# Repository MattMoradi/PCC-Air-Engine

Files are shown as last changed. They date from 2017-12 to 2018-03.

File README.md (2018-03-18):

# PCC-Air-Engine

Tired of those darn old hand drawn designs for the PCC Air Engine project? Think you deserve better? Well here you are.

This repository contains all of the necessary files for the PCC Air Engine project from designs to gcode. All CAD modeling and CAM toolpathing was done using Autodesk Inventor HSM. Special thanks to Autodesk for providing this software free to students. All NC code has been optimized to run on the HAAS Mini-Mill 2005. This also contains the new standardized digital drawing file format and has replaced the previous hand drawn ones at Glencoe.

### Included Parts & Formats: ###

* Standard: CAD + CAM + DWG + PDF + CNC
* Standard_Bushing: CAD
* Piston_Bushing: CAD
* Piston: CAD + DWG + PDF
* Piston_Block (Cylinder): CAD + CAM + DWG + PDF + CNC
* Flywheel: CAD + DWG + PDF
* Crankshaft: CAD + DWG + PDF
* Air_Engine_Full: CAD + ASM

### PCC Credits Covered ###
* CRN: 11691 - MCH100-0
* CRN: 11691 - MCH135-0
* CRN: 11692 - MCH145-0
* CRN: 11964 - MCH150-0
* CRN: 11693 - MCH160-0
* CRN: 11694 - MCH180-0
* CRN: 11965 - MCH205-0

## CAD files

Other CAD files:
DWG Drawings/Flywheel_Draw.dwg
DWG Drawings/CrankShaft_Draw.dwg
DWG Drawings/Piston_Block_Draw.dwg
DWG Drawings/Piston_Draw.dwg
DWG Drawings/Standard_Draw.dwg
OldVersions/Piston_Draw.0006.dwg
OldVersions/Flywheel_Draw.0004.dwg
OldVersions/Standard_Draw.0020.dwg
OldVersions/CrankShaft_Draw.0005.dwg
OldVersions/Piston Block_Draw.0007.dwg
Air_Engine_ASM.iam
CrankShaft.ipt
CrankShaft_Mill.ipt
Flywheel.ipt
OldVersions/Air_Engine_ASM.0010.iam
OldVersions/CrankShaft Mill.0001.ipt
OldVersions/CrankShaft.0006.ipt
OldVersions/CrankShaft_Mill.0002.ipt
OldVersions/Flywheel.0003.ipt
OldVersions/Main Block.0001.ipt
OldVersions/Piston Block.0011.ipt
OldVersions/Piston.0002.ipt
OldVersions/Standard.0026.ipt
Piston.ipt
Piston_Block.ipt
Piston_Bushing.ipt
Standard.ipt
Standard_Bushing.ipt

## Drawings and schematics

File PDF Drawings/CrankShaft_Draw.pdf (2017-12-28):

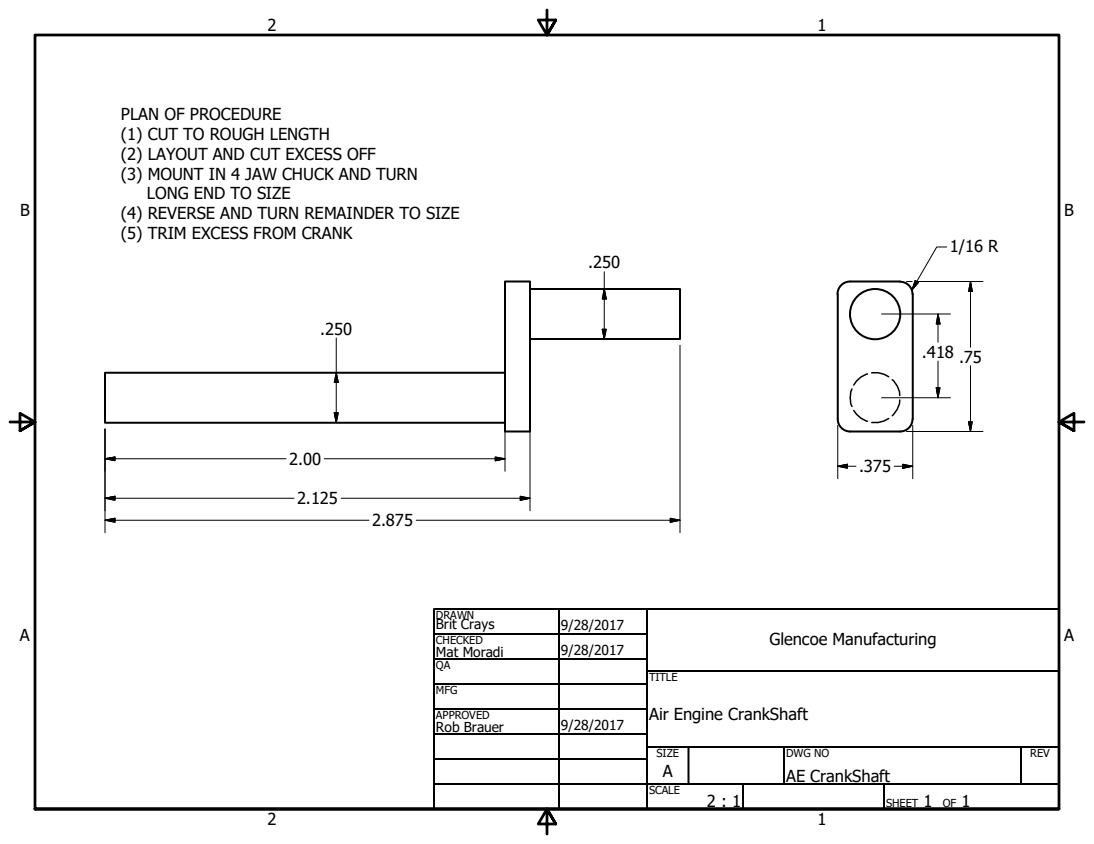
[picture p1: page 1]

PLAN OF PROCEDURE
(1) CUT TO ROUGH LENGTH
(2) LAYOUT AND CUT EXCESS OFF
(3) MOUNT IN 4 JAW CHUCK AND TURN
LONG END TO SIZE
(4) REVERSE AND TURN REMAINDER TO SIZE
(5) TRIM EXCESS FROM CRANK

DRAWN Brit Crays | 9/28/2017 | Glencoe Manufacturing

CHECKED Mat Moradi | 9/28/2017

MFG

APPROVED Rob Brauer | 9/28/2017

Air Engine CrankShaft

SIZE A | DWG NO AE CrankShaft | REV

SCALE 2 : 1 | | SHEET 1 OF 1

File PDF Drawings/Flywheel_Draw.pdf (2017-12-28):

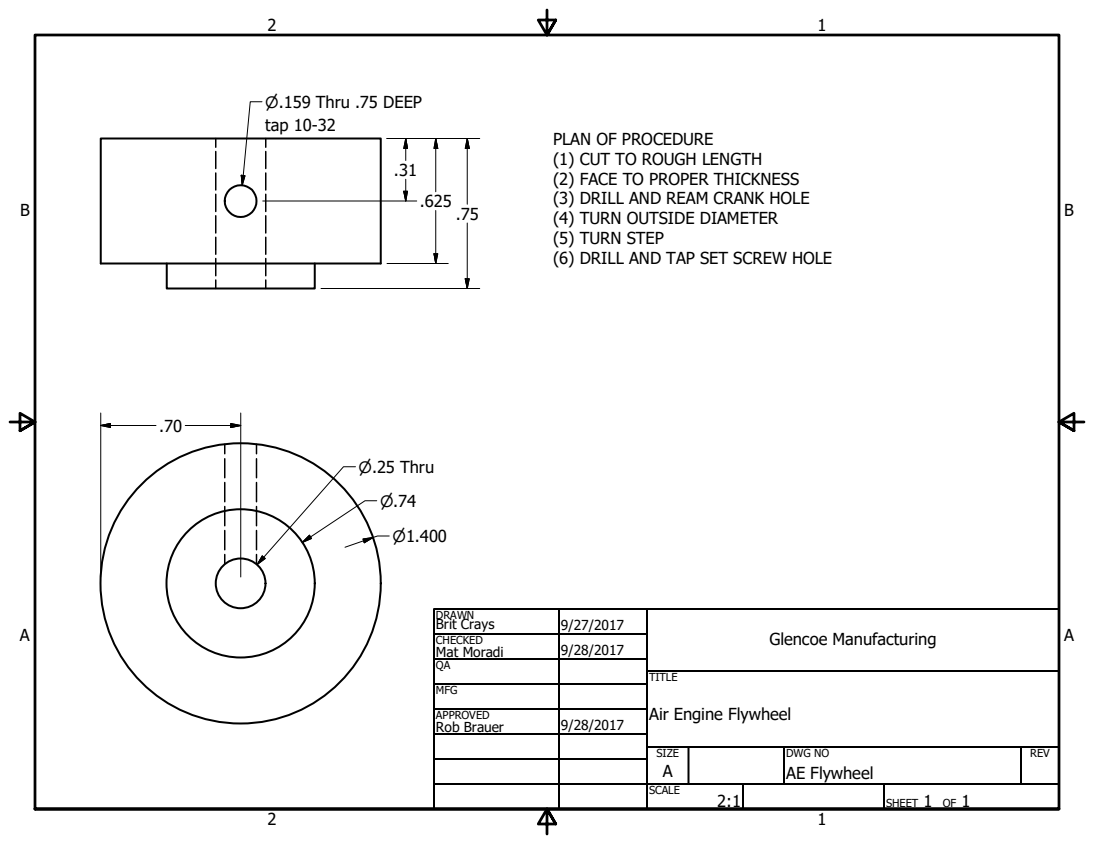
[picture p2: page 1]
tap 10-32

PLAN OF PROCEDURE
(1) CUT TO ROUGH LENGTH
(2) FACE TO PROPER THICKNESS
(3) DRILL AND REAM CRANK HOLE
(4) TURN OUTSIDE DIAMETER
(5) TURN STEP
(6) DRILL AND TAP SET SCREW HOLE

DRAWN Brit Crays | 9/27/2017 | Glencoe Manufacturing

CHECKED Mat Moradi | 9/28/2017

MFG

APPROVED Rob Brauer | 9/28/2017

Air Engine Flywheel

SIZE A | DWG NO AE Flywheel | REV

SCALE 2:1 | | SHEET 1 OF 1

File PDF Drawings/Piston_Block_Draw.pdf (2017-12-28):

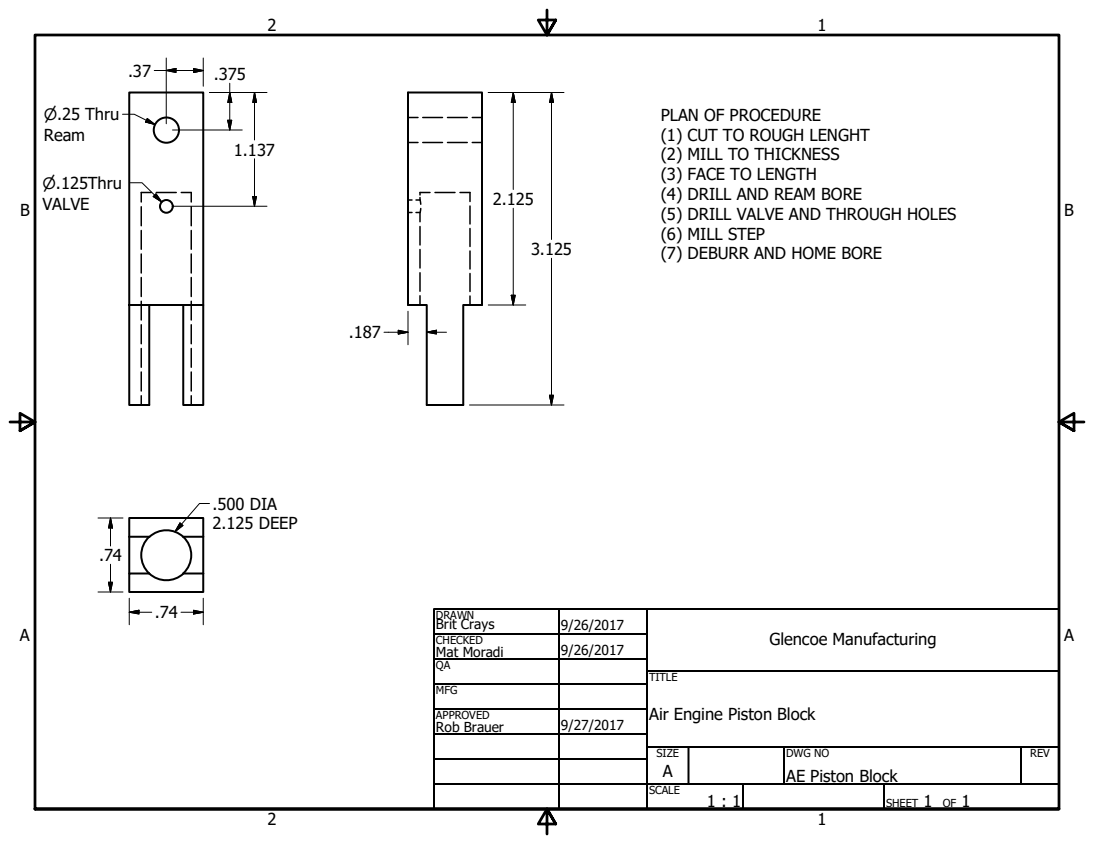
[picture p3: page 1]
.500 DIA 2.125 DEEP

PLAN OF PROCEDURE
(1) CUT TO ROUGH LENGHT
(2) MILL TO THICKNESS
(3) FACE TO LENGTH
(4) DRILL AND REAM BORE
(5) DRILL VALVE AND THROUGH HOLES
(6) MILL STEP
(7) DEBURR AND HOME BORE

DRAWN Brit Crays | 9/26/2017 | Glencoe Manufacturing

CHECKED Mat Moradi | 9/26/2017

MFG

APPROVED Rob Brauer | 9/27/2017

Air Engine Piston Block

SIZE A | DWG NO AE Piston Block | REV

SCALE 1 : 1 | | SHEET 1 OF 1

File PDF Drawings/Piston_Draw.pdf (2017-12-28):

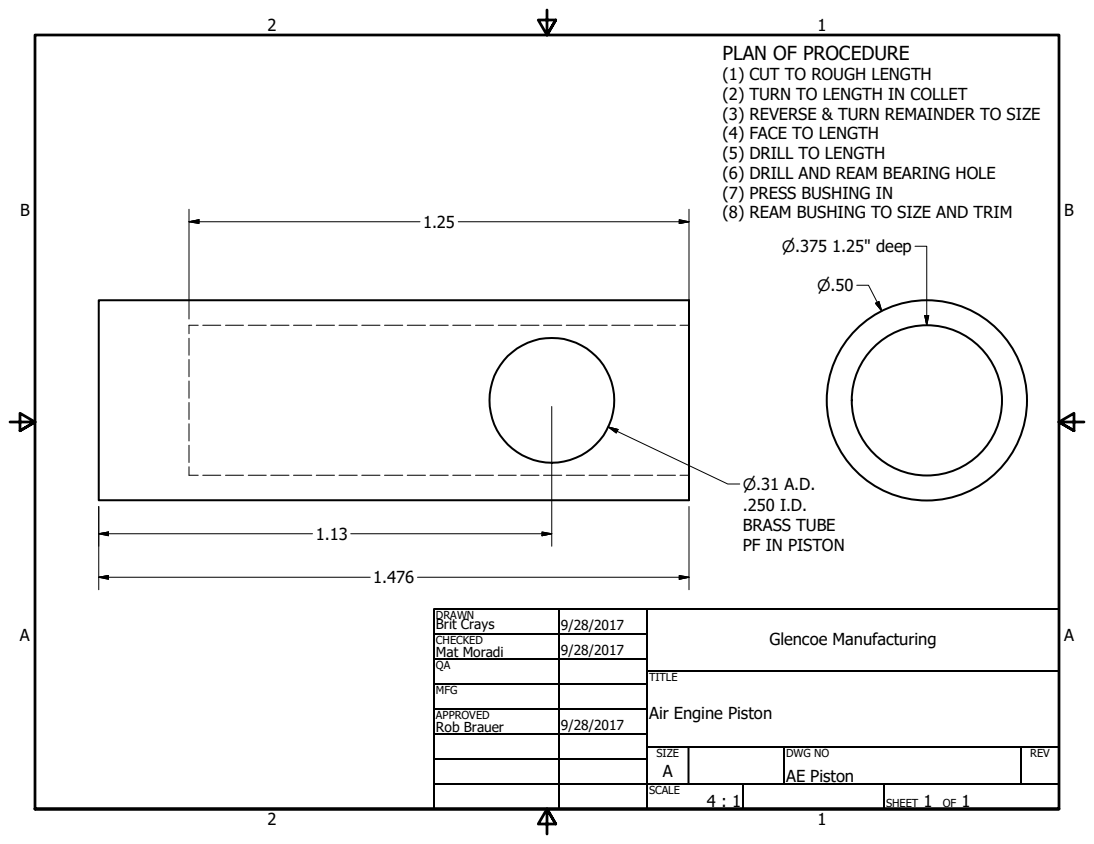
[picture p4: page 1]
.250 I.D. BRASS TUBE PF IN PISTON

PLAN OF PROCEDURE
(1) CUT TO ROUGH LENGTH
(2) TURN TO LENGTH IN COLLET
(3) REVERSE & TURN REMAINDER TO SIZE
(4) FACE TO LENGTH
(5) DRILL TO LENGTH
(6) DRILL AND REAM BEARING HOLE
(7) PRESS BUSHING IN
(8) REAM BUSHING TO SIZE AND TRIM

DRAWN Brit Crays | 9/28/2017 | Glencoe Manufacturing

CHECKED Mat Moradi | 9/28/2017

MFG

APPROVED Rob Brauer | 9/28/2017

Air Engine Piston

SIZE A | DWG NO AE Piston | REV

SCALE 4 : 1 | | SHEET 1 OF 1

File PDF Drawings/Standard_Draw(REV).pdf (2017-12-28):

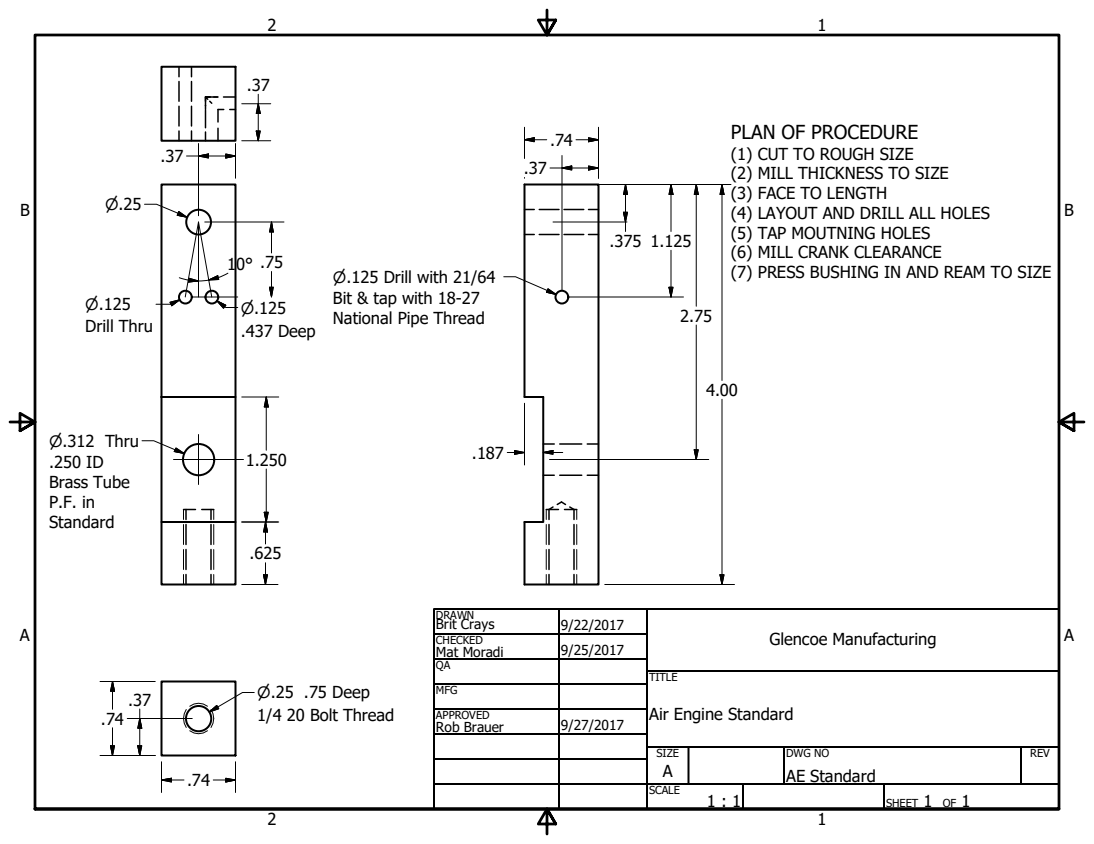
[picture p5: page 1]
1/4 20 Bolt Thread; Drill Thru; .437 Deep; .250 ID Brass Tube P.F. in

PLAN OF PROCEDURE
(1) CUT TO ROUGH SIZE
(2) MILL THICKNESS TO SIZE
(3) FACE TO LENGTH
(4) LAYOUT AND DRILL ALL HOLES
(5) TAP MOUTNING HOLES
(6) MILL CRANK CLEARANCE
(7) PRESS BUSHING IN AND REAM TO SIZE

.125 Drill with 21/64
Bit & tap with 18-27
National Pipe Thread

DRAWN Brit Crays | 9/22/2017 | Glencoe Manufacturing

CHECKED Mat Moradi | 9/25/2017

MFG

APPROVED Rob Brauer | 9/27/2017

Air Engine Standard

SIZE A | DWG NO AE Standard | REV

SCALE 1 : 1 | | SHEET 1 OF 1

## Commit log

2017-12-28 Initial Commit With CAD Drawing Files
    Contains both the DWG and PDF formats for the CAD drawings.
    [Air_Engine_ASM.0008.iam, CrankShaft.0006.ipt, CrankShaft_Draw.0005.dwg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]
2018-01-02 Initial Commit of CAD Model Files
    Contains the 3D models for the part files.
    [Flywheel.ipt, Piston Bushing.ipt, Piston.ipt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]
2018-01-02 Completed CAD + CAM + CNC Procedures 4 Standard
    [Standard.ipt]
2018-01-16 Completed CAD + HSM Procedures 4 Cylinder
    [Piston Block.ipt]
2018-01-31 Added CrankShaft CAD
    [CrankShaft.ipt]
2018-02-02 Added AirEngine Assembly
    [Air_Engine_ASM.iam]
2018-02-06 Alternate Crankshaft CAM
    Created an alternate CAD file for milling procedures since the geometry of the original is not valid for CAM.
    [CrankShaft Mill.0001.ipt, CrankShaft Mill.ipt]
2018-02-06 Fixed Naming Conventions
    This was bothering me...
    [CrankShaft_Mill.ipt, Piston_Block.ipt, Piston_Bushing.ipt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]
2018-03-01 Added Crankshaft HSM
    [CrankShaft_Mill.0002.ipt, CrankShaft_Mill.ipt]
2018-03-16 Fixed Piston Mount In ASM
    Apparently the piston was mounted upside down. Also added some textures.
    [Air_Engine_ASM.0008.iam, Air_Engine_ASM.0010.iam, Air_Engine_ASM.iam]
2018-03-18 Added PDF To Cylinder Listing
